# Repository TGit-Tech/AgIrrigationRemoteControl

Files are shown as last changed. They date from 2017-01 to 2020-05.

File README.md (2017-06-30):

# AgIrrigationRemoteControl
Control an Ag Industrial 3-Phase Irrigation Pump with Arduino UNO and XBee RF

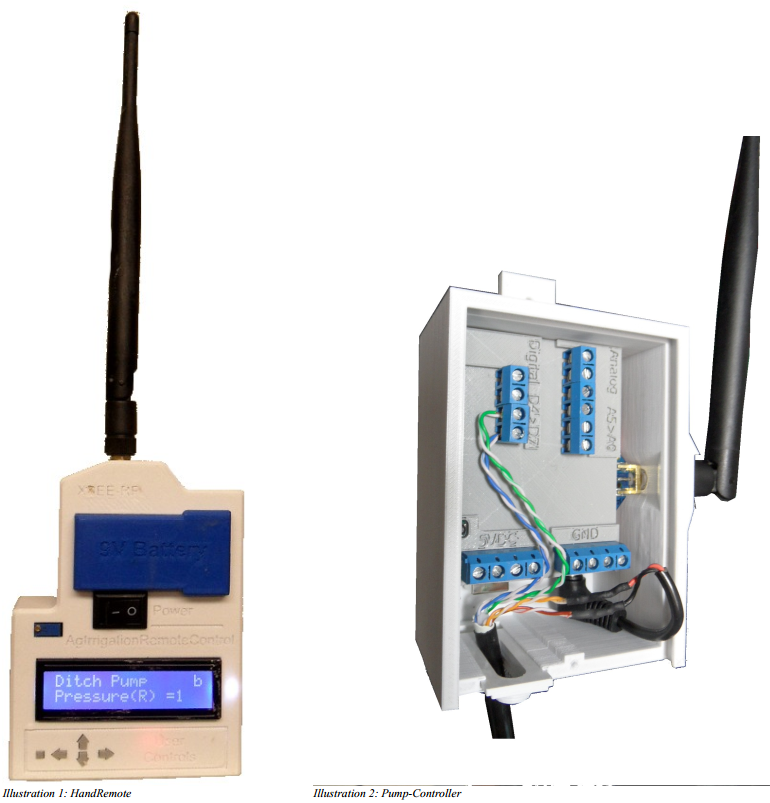
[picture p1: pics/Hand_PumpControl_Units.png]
Hand Remote

# Overview
- A solid rural 2-Mile range; possibly more ( 900MHz @ 1/4-Watt Transceiver )
- No cellular, FCC liscensing or any other charges; Just hook it up and use
- One Hand-Remote can control multiple irrigation pumps
- Multiple Hand-Remotes can control one irrigation pump
- Uses Pump Panels "AUTO" selection; doesn't disturb Manual Hand-Off & Start sequences
- Implements a "stay-off" after a power loss that is required by power companies
- Hand-Remote has settable Alarms that signal (via buzzer) unexpected conditions such as:
    - Power not as expected ( Alarms when pump shutdown has occured by a power loss )
    - Water Pressure ( if equipped ) for when a hose falls off
    - Ditch Water Level ( if equipped ) too high or low
- Simple expansion of a digital pressure gauge for water pressure monitoring
- Simple expansion of an Ultrasonic distance meter for water level monitoring

# I'll Build one for you!
I'll be building a few of these units complete with
- (1) Hand-Remote; Custom programmed to your irrigation setup
- (1) Pump-Controller; Custom programmed to your irrigation setup
- (1) Installation Kit including:
    - The required 480VAC 3-phase Power Supply
    - A 480VAC or higher Solid State Relay for Motor Starter Control
    - 600V THHN Hook-Up wire required to Motor control installation

Purchase for $329 at: https://www.etsy.com/listing/525674784/agriculture-3-phase-480vac-irrigation

If you'd like to purchase just a single unit or the Water-Level and Pressure expansion kits; you can email me directly at tgit28@gmail.com

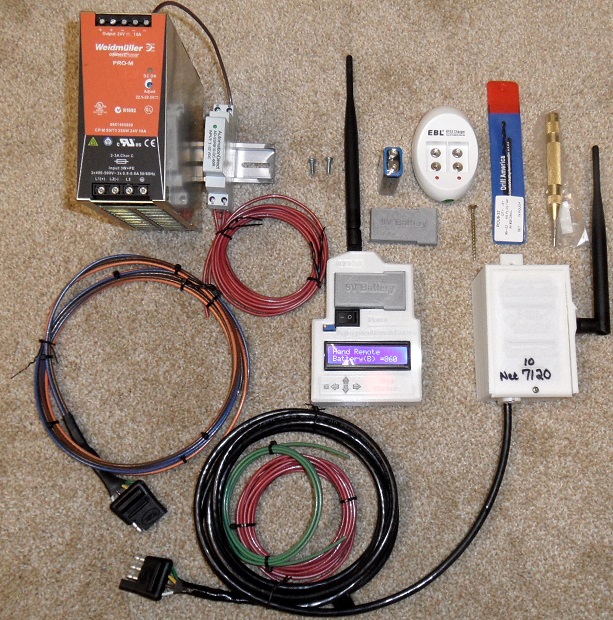
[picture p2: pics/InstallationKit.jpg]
Installation Kit


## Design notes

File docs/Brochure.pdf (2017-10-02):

# Agriculture Irrigation Pump RF Remote Control Kit

Save time changing water by Turning On and Off your irrigation pump remotely.

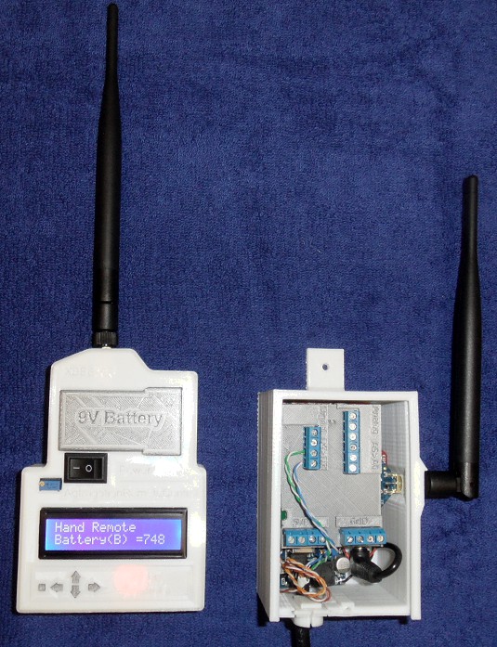
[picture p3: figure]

- Switch the pump off from the comfort of your home and wait for lines to drain before leaving.
- On the spot; Switch pump off and disconnect wheel line ends.

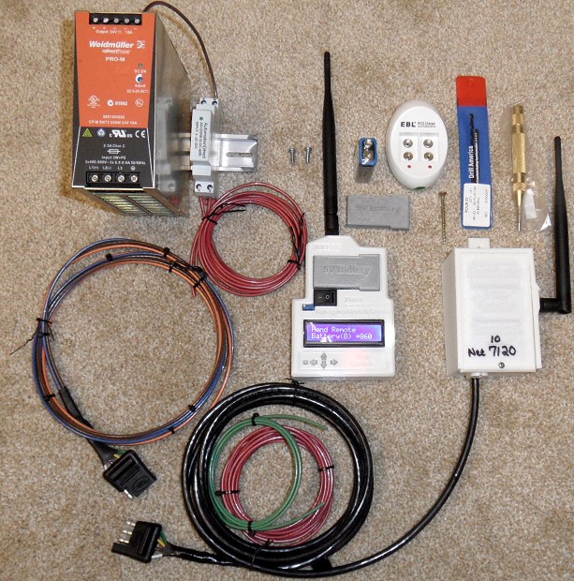
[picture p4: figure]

- Switch the pump on just as soon as
water change is complete
- On the spot pump switching for leaky drains and stubborn plugs. Simple Installation Procedure

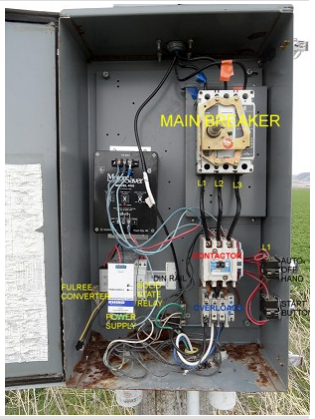
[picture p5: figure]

- Power Supply Hookup
- Solid State Relay Hookup
- Pole Mount Transceiver
- Plug-in Transceiver
- Done!

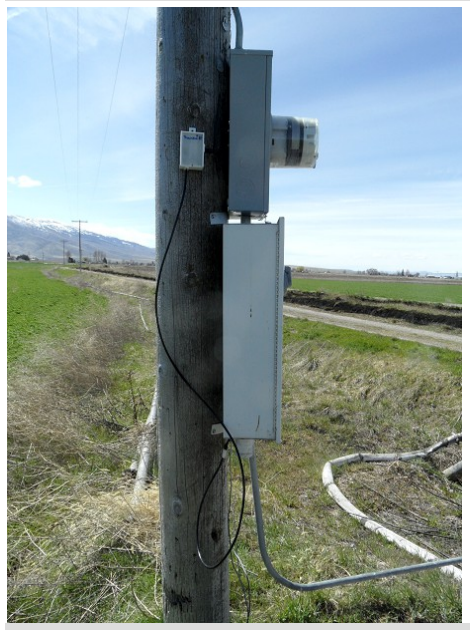
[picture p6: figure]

Easy expansion to monitor the pump 24/7
- Monitor the Water Pressure
- Monitor the Ditch Water Level
- Alarm on remote will activate when either is out of bounds.
- Special custom designs are available to suit your needs

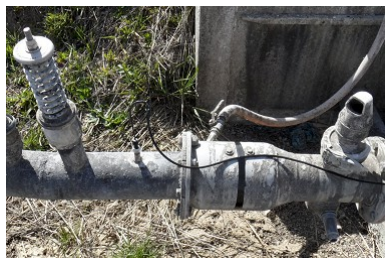
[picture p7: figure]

-----------------------------------------------------------------------------------------------------------------------------Detailed User and Installation Manual @ https://tgit23.github.io/AgIrrigationRemoteControl/manual/ Order Yours @ https://www.etsy.com/listing/525674784/irrigation-pump-remote-control-480vac-3

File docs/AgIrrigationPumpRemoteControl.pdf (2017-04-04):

# Ag Irrigation-Pump Remote Control

## Using Arduino-UNO and Digi-Xbee RF

Written By: Thomas G (01/2017) Feel free to use: no strings attached (text content only / images respectfully referenced)

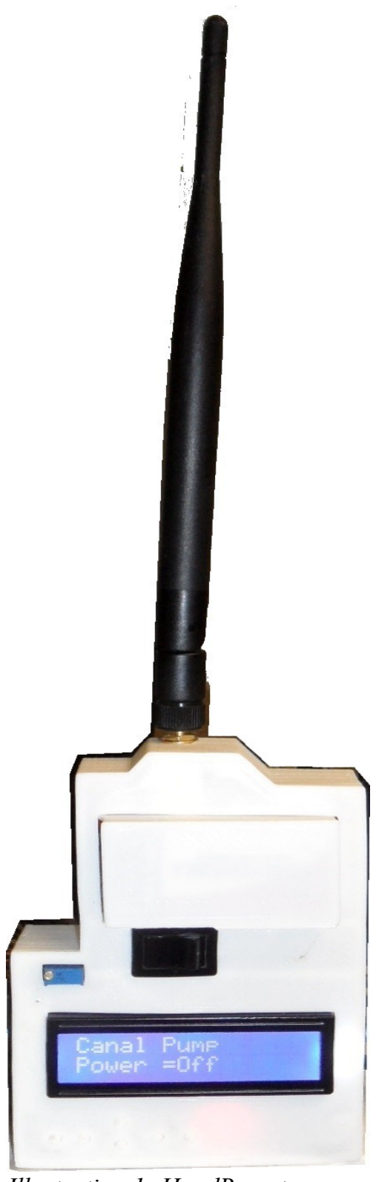
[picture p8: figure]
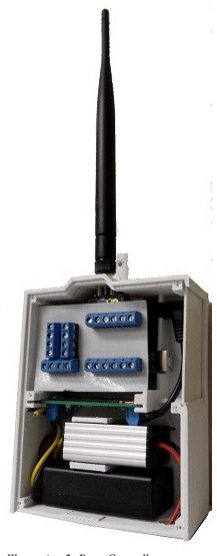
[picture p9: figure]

Illustration 1: HandRemote | Illustration 2: PumpController

# Table of Contents

( 1. INTRODUCTION :: INTRODUCTION :: INTRODUCTION ) Page -3-

### 1. INTRODUCTION

The “Ag Irrigation Pump Remote Control” project's goal is to provide RF remote control and monitoring features of an Agriculture-Industry Irrigation Pump; typically used in wheel-line and hand-line irrigation setups. The project uses Xbee RF radio's with up to a 28-mile range ( More practically a mile or two at ground level ). The project consists of a Hand-Held “Hand Remote” and a pole mounted “Pump Controller” as well as high voltage control electrical components to be added inside the pumps electrical panel.

✔ The project is Open Source and Resides at: https://github.com/tgit23/AgIrrigationRemoteControl
✔ The most recent version of this document is at: https://github.com/tgit23/AgIrrigationRemoteControl/docs/AgIrrigationPumpRemoteControl.pdf

### 1.1 Bill Of Materials (BOM) - $267.66

A. Pump-Panel Components ( $95.74 )
Illustration 3: (1) Power Supply | Illustration 4: (1) Solid State Relay | Illustration 5: (1) DIN Rail

◌ (1) 12VDC Power Supply – Main power for each PUMPCONTROLLER
- Buying Options ( Recommended; the RHINO & Fulree Converter for practical usage and pricing )
- RHINO switching Power supply, 24 VDC output, 2.5A, 60W, 320-600 VAC input, 3-phase, 35mm DIN rail mount.
- https://www.automationdirect.com/adc/Shopping/Catalog/Power_Products_(Electrical)/DC_Power_Supplies/24VDC,_3-Phase_Input/PSB24-060S-3 ( $59.00/EA )
- RHINO Requires; ( 24 12VDC ) Fulree Converter ( → | see Electronic Control Section below ) ( $7.99/EA )
- TDK Lamda Rail Power Supplies 120W 12V 10A DIN Rail 380-480VAC
- www.mouser.com/ProductDetail/TDK-Lambda/DPP120-12-3/ ( $104.04/EA )

◌ (1) Solid state relay, 35mm DIN-rail, 3-32 VDC input, SPST, normally open SCR, 10A contact rating, 48-480 VAC load voltage – for each Pump
- https://www.automationdirect.com/adc/Shopping/Catalog/Relays_-z-_Timers/Solid_State_Relays/DIN_Mount_Relays_(AD-SSR8_-z-_AD-SSR2_-z-_AD-SSR6_-z-_AD-HSSR8_Series)/Gen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,_(AD-SSR8_-z-_AD-SSR2_-z-_AD-SSR6_Series)/AD-SSR810-DC-48Z (https://www.automationdirect.com/adc/Shopping/Catalog/Relays_-z-_Timers/Solid_State_Relays/DIN_Mount_Relays_(AD-SSR8_-z-_AD-SSR2_-z-_AD-SSR6_-z-_AD-HSSR8_Seri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) ( $20.75/EA )

◌ (1) 6” of DIN rail, slotted, 35mm, 10 mm height – for mounting Power Supply and Solid State Relay of each Pump
- https://www.automationdirect.com/adc/Shopping/Catalog/Enclosures_-z-_Subpanels_-z-_Thermal_Management_-z-_Lighting/Enclosure_Subpanels_-a-_Internal_Mounting_Accessor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 (https://www.automationdirect.com/adc/Shopping/Catalog/Enclosures_-z-_Subpanels_-z-_Thermal_Management_-z-_Lighting/Enclosure_Subpanels_-a-_Internal_Mounting_A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) ( $8.00/2x 1-Meter Pieces )
B. Electronic Control ( $39.10 )
Illustration 6: (2) Arduino UNO R3 | Illustration 7: (1) LCD Keypad Shield | Illustration 8: (2) Zigbee Shield

◌ (2) UNO R3 Atmega328P Development Board with Male Pin Header and USB Cable - (1) for each HANDREMOTE and (1) for each PUMPCONTROLLER

( 1.1 INTRODUCTION :: Bill Of Materials (BOM) - $267.66 :: Bill Of Materials (BOM) - $267.66 ) Page -4-

- https://www.aliexpress.com/item/Free-shipping-high-quality-UNO-R3-MEGA328P-CH340-CH340G-for-Arduino-UNO-R3-USB-CABLE/32353698284.html ( $3.80/ea )

◌ (1) Keypad Shield Blue Backlight for Arduino Robot LCD 1602 Board – Display for each HANDREMOTE
- https://www.aliexpress.com/item/Free-Shipping1PCS-LCD-Keypad-Shield-LCD1602-LCD-1602-Module-Display-for-arduino-ATMEGA328-ATMEGA2560-raspberry-NO/32787414048.html ( $2.19 / ea )
- DFRobot Wiki LCD @ https://www.dfrobot.com/wiki/index.php/Arduino_LCD_KeyPad_Shield_(SKU:_DFR0009)
- Schematic @ http://image.dfrobot.com/image/data/DFR0009/LCDKeypad%20Shield%20V1.0%20SCH.pdf
- Layout @ https://raw.githubusercontent.com/Arduinolibrary/DFRobot_LCD_keypad/master/DFR0009_Layout.png

◌ (2) Zigbee Shield RF Wireless Module Expansion Board for Arduino Xbee - (1) for each HANDREMOTE and (1) for each PUMPCONTROLLER
- http://www.banggood.com/Zigbee-Shield-RF-Wireless-Module-Expansion-Board-For-Arduino-XBee-p-916226.htm l ( $4.83/ea )
- Schematic @ https://www.arduino.cc/en/uploads/Main/XbeeShieldSchematic.pdf
- Tutorial @ https://www.cooking-hacks.com/documentation/tutorials/xbee-arduino-raspberry-pi-tutorial/

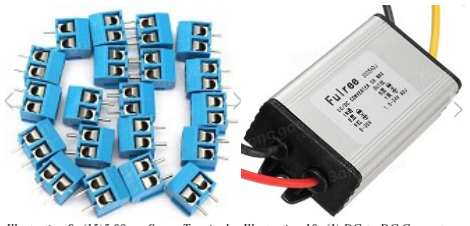
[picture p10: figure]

Illustration 9: (15)5.08mm Screw Terminal Illustration 10: (1) DC-to-DC Converter

◌ (15) 2x Pin Plug-in Screw Terminal Block Connector 5.08mm Pitch - External I/O connections for each PUMPCONTROLLER
- http://www.banggood.com/20pcs-2-Pin-Plug-in-Screw-Terminal-Block-Connector-5_08mm-Pitch-p-993197.html ( $2.15 / 20pcs )

◌ (1) Fulree DC 8-35V to 1.5-24V Adjustable Buck Converter Power Supply Voltage Regulator – For the RHINO Power Supply purchase ONLY
- http://www.banggood.com/DC-8-35V-to-1_5-24V-Adjustable-Buck-Converter-Power-Supply-Voltage-Regulator-For-Car-Truck-Boat-p-1087176.html ( Price listed with Pump Panel )
Illustration 11: Female Pin Headers | Illustration 12: Rocker Switch | Illustration 13: Active Buzzer Illustration 14: 50 / 30cm x 70cm Perfboard

◌ (4) Pin Headers 2.54mm pitch - For each PUMPCONTROLLER
- (1) 4-PIN Male | - Zigbee->Perfboard POWER ( $NA / Included with Arduino Kit - Male headers can be cut to length )
- (2) 6-PIN Male | - Zigbee->Perfboard (1) for Analog (1) for Digital ( $NA )
- (1) 4-PIN Female | - Zigbee->Perfboard RX/TX
- https://www.aliexpress.com/item/10-pcs-4P-4pin-Female-Single-Row-Straight-Header-Strip-Socket-Connector-Pitch-2-54mm/32442087495.html ( $0.79 / 10pcs )

◌ (1) Black Snap-in On/Off Rocker Switch – For each HANDREMOTE
- https://www.aliexpress.com/item/New-Black-Push-Button-Mini-Switch-6A-10A-110V-250V-KCD1-2Pin-Snap-in-On-Off/32670615106.html ( $0.86 / 5pcs )

◌ (1) Active Speaker Buzzer Alarm – For each HANDREMOTE
- https://www.aliexpress.com/item/KEYES-KY-012-Active-Buzzer-Module-FOR-The-ARDUINO-AVR-PIC/32740686896.html ( $0.60 / ea )

◌ (1) FR-4 Double Side 50cm x 70cm Prototype PCB Printed Circuit Board - (1) 50cm x 70cm for each PUMPCONTROLLER
- https://www.aliexpress.com/item/Free-Shipping-4pcs-5x7-4x6-3x7-2x8-cm-double-Side-Copper-prototype-pcb-Universal-Board-for/32730636287.html ( $1.56/ 4pcs )

( 1.1 INTRODUCTION :: Bill Of Materials (BOM) - $267.66 :: Bill Of Materials (BOM) - $267.66 ) Page -5-

◌ (2) Resistors; One valued at 1/3 the other - Recommend above 10K-Ohms – (2) for each HANDREMOTE
- http://www.banggood.com/300Pcs-1-14W-Metal-Film-Resistor-Resistance-30-Values-Assortment-Kit-p-1091920.html ( $2.28 / 300pcs )

◌ (1) Right-Angle 9Vdc Power Plug for Arduino Power Jack
- https://www.amazon.com/gp/product/B0111M6PIQ/ ( $4.51 / 10pcs )

◌ (1) Computer power connector
- http://www.banggood.com/CPU-Fan-4Pins-Patch-Cord-to-34-Pins-Power-Adapter-Cable-Lead-Wire-p-998249.html ( $1.99 / ea )

◌ (5) #4 Small Screws no longer than 10mm or bigger than 3.5mm for Display and Case covers
- https://www.boltdepot.com/Sheet_metal_screws_Phillips_pan_head_Zinc_plated_steel_4.aspx ( $0.05/ea )
C. RF Electronics ( $80.88 )

◌ (2) Xbee-Pro 900Hp S3B Digimesh, 900Mhz, 250Mw, Rpsma Connector, 200Kbps – (1) for each HANDREMOTE and (1) for each PUMPCONTROLLER
- https://www.arrow.com/en/products/xbp9b-dmst-002/digi-international ( $36.11/EA )

◌ (2) Antenna Helical 3dB Gain 900MHz – (1) for each HANDREMOTE and (1) for each PUMPCONTROLLER
- https://www.arrow.com/en/products/w1063/pulse-electronics-corporation ( $4.33/ea )
D. Wire ( $51.94 )

◌ (~10-feet) 600V 12-AWG wire for all “Inside” the Pump Panel power supply and control wiring – Enough to connect RHINO P.S., SSR and Exit Panel
- https://www.amazon.com/GREEN-12AWG-Stranded-600V-Hook/dp/B005643KCK/ref=sr_1_ 3 ( $21.99 / 25ft )

◌ (~30-feet) 24-AWG outdoor direct burial wire for Pump-Controller wiring – Enough to connect all accessory/power devices to the Pump-Controller
- https://www.amazon.com/BULKRAW-Outdoor-Outside-Waterproof-Cable/dp/B00C2J04KS/ref=sr_1_4 ( $29.95 / 40ft )

( 1.1 INTRODUCTION :: Bill Of Materials (BOM) - $267.66 :: Bill Of Materials (BOM) - $267.66 ) Page -6-

E. Tools Required ( $NA )

◌ 3D-Printer ( may be optional if other casing solutions are available ) ◌ Soldering Iron / Solder / Connecting Wire
◌ Screw Driver

### 2. HAND-REMOTE

The HANDREMOTE is the remote controller unit used to control and monitor an irrigation pump remotely.

✔ Features
◌ Buzzer alarm settings for monitored values
◌ Battery level indicator ( 9V-Battery Powered )
◌ Programmable Interface through USB

### 2.1 Electronics Assembly

✔ The HANDREMOTE uses the following electronic parts ◌ 1- Arduino UNO R3 Board
◌ 1- LCD Keypad Shield
◌ 1- Zigbee Shield
◌ 1- Xbee-Pro 900Hp S3B Module and High Gain Helical Antenna ◌ 1- 9Vdc Battery Connector
◌ 1- Active Buzzer
◌ 2- Resistors

( 2.1 HAND-REMOTE :: Electronics Assembly :: Electronics Assembly ) Page -7-

A. LCD Keypad Shield
1. Wire the Battery-Meter Voltage-Divider
a) Select (2) Resistors; One-Value being 1/3 the other ( 10K-ohm up to 1M-ohm is recommended )
b) Solder First Resistor ( Full Value ) on the top of the LCD Shield from VIN A1 →
c) Solder Other Resistor ( 1/3 Value ) from A1 GND → ( Solder hole just left of VIN )
d) Snip off the excess back-side leads

The two resistors setup a voltage divider from the 9Vdc battery (which we will attach to VIN). Analog inputs on the Arduino should never exceed 5Vdc. The voltage divider will split the battery voltage to 1/3 its actual voltage. This will allow the hand-remote to monitor the battery level. The larger the resistor values the less drain on the battery; but too-large a value resistors may affect accuracy.

2. Plug the LCD Keypad Shield onto the Arduino UNO
B. Zigbee/Xbee Shield
1. Remove Header Pin D7 From Zigbee Shield
a) Using Needle Nose pliers clamp onto Pin D7 of the back of the Zigbee Shield
b) Using Soldering Iron – Heat the top of the pins solder pad and pull the pin from the board

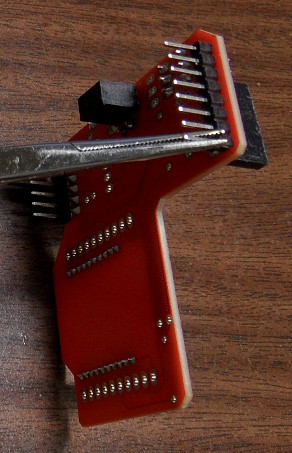
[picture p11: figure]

2. Solder Zigbee Shield to the LCD Keypad ( Flipped upside down )
a) Insert pins D0 D6 ( D7 removed in Step #1 ) into the Top Solder holes of the LCD Keypad Shield →
b) Position the Zigbee Shield flat with LCD Shield and Up against the LCD Shield – Requires bending the header pins a little ( with UNO Attached )
c) Solder the Zigbee pins to the LCD Keypad Shield

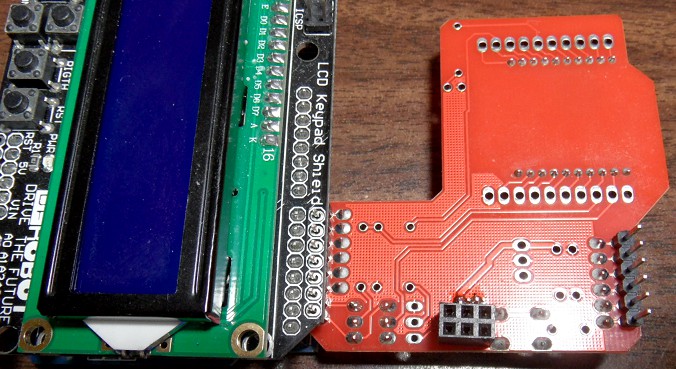
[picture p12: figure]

( 2.1 HAND-REMOTE :: Electronics Assembly :: Electronics Assembly ) Page -8-

✔ Further Reading for the Curious
- https://www.arduino.cc/en/Main/ArduinoXbeeShield
- https://www.arduino.cc/en/Guide/ArduinoXbeeShield
C. Active Buzzer
1. Solder Active Buzzer to LCD Keypad Shield
a) Either print a small piece of plastic or add Black tape to the Back-Side of the Active Buzzer to prevent shorting against the Zigbee Shield.
b) Solder the 'S' pin on the Active Buzzer to D2 ( 3rd Left Pin – LCD Face Up ) on the LCD Shield
c) Cut the (-) and center pins of the Active Buzzer leaving about 1/8” for connection but short enough not to touch D3 & D4.

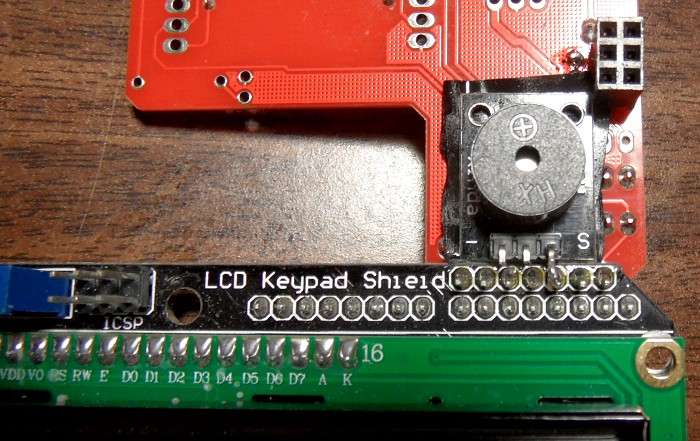
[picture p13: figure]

( 2.1 HAND-REMOTE :: Electronics Assembly :: Electronics Assembly ) Page -9-

2. Wire Power to the Active Buzzer and Zigbee Shield
a) Bend the first and last pins closest to the edge of the LCD Keypad Shields ICSP pin header
b) Solder one end of a Red wire Left-Most Pin of the LCD Keypad Shields ICSP pin header ( → | 5V+)
- Pull wire to Active Buzzer (+) Pin ( Center Pin ), strip insulation and solder
- Pull wire to Lower-Right of the Zigbee ICSP ( 5V+ ) plug, strip insulation, cut to length and insert into plug
c) Solder one end of a Black wire Right-Most Pin of the LCD Keypad Shields ICSP pin header ( → | 5V+)
- Pull wire to Active Buzzer Left-Pin (-), strip insulation and solder
- Pull wire to Top-Right of the Zigbee ICSP ( GND ) plug, strip insulation, cut to length and insert into plug

Red/Black wires were not cut but the insulation was split using automatic wire strippers. The Center and Left Pins of the Buzzer were cut just long enough to solder wires to them.

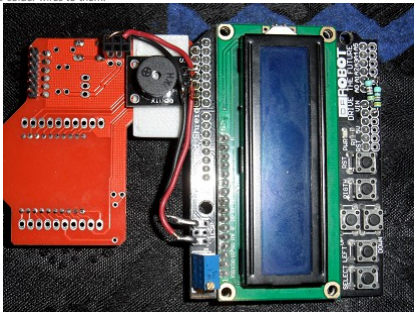
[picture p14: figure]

3. Cut the remaining ICSP pins as short as possible to allow the unit to fit inside the case
D. Communications

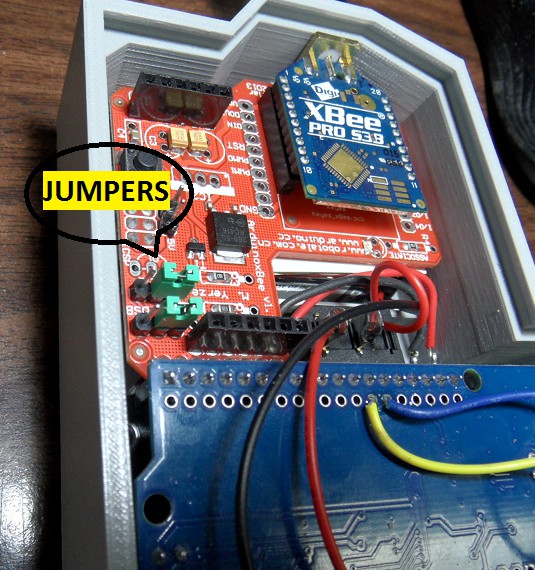
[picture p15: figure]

1. Remove the two green jumpers factory installed on the Zigbee shield

( 2.1 HAND-REMOTE :: Electronics Assembly :: Electronics Assembly ) Page -10-

2. Connect Arduino UNO pins D11 & D12 to the Zigbee Communication Header
a) From an upside-down view; left-top of Arduino UNO; Count the pin holes to the right D0,D1,D2.... to D11
b) Solder a wire from Arduino UNO pin D11 to the top-jumper-header center-pin of the Zigbee shield
c) Solder a second wire from Arduino UNO pin D12 to the bottom-jumper-header center-pin of the Zigbee shield

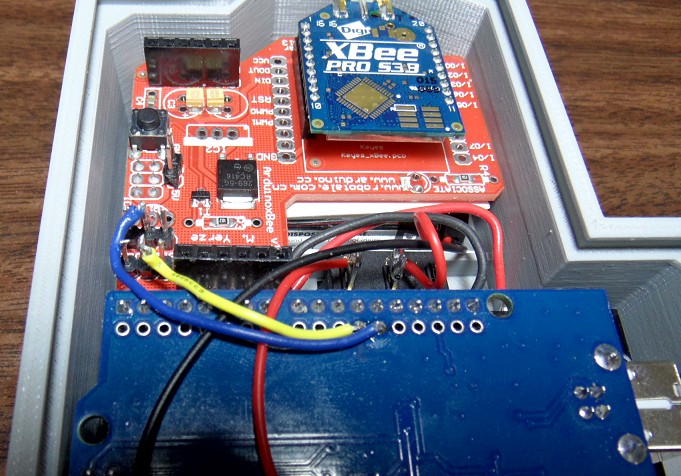
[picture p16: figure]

✔ Further Details for the Curious

◌ Xbee and Arduino both use Serial Communications –- but they both cannot use the same Serial Port at the same time.
- In order to Upload Firmware to the Arduino the Xbee must be disconnected from the lines ( No Jumpers )
- In order to Connect to the Xbee through USB Serial the Arduino Microcontroller must be disconnected ( UN-usable for our Arduino UNO )
- Thus; We add Jumper-wires to put the Xbee on a different “Serial Port” when we need access to both Serial Devices.

◌ The Factory Jumpers on the Zigbee Shield come with two modes of operations
- Xbee Position = Xbee UART Serial connects to Arduino Serial
- USB Position = Xbee UART Serial connects to USB Serial ( Computer ); Requiring the removal of the micro-controller.

◌ Jumper-Wires for Debug
- Computer USB Serial Arduino → | - When NO jumpers exist; the Xbee is disconnected from RX/TX Pins and thus allows clean USB Serial Monitor.
- Routes Xbee UART D11 & D12 → | - The SOFTWARESERIAL Library allows UART communications on D8 & D9 which is wire-jumped to the Xbee RX/TX.

◌ Pin Orientation
- The Jumpers on the Zigbee Shield are aligned Top->Bottom Exactly the same as the Xbee Plug labeled DIN/DOUT are aligned
- On the shield (DIN is the closest jumper to Digital Pins Header on the Shield)

( 2.2 HAND-REMOTE :: Hardware Assembly :: Hardware Assembly ) Page -11-

### 2.2 Hardware Assembly

A. 3D-Prints
✔ Print the Following Models on a 3D-Printer
◌ /HandRemote/3D-Prints-STL/HandRemote-Case.stl
◌ /HandRemote/3D-Prints-STL/HandRemote-Buttons.stl
◌ /HandRemote/3D-Prints-STL/HandRemote-BackCover.stl
◌ /HandRemote/3D-Prints-STL/HandRemote-BatteryCover.stl
◌ /HandRemote/3D-Prints-STL/HandRemote-BatteryInsulatorPlate.stl ◌ /HandRemote/3D-Prints-STL/HandRemote-SideCover.stl
Illustration 15: Case.stl | Illustration 16: BackCover.stl | Illustration 17: Battery Cover
Illustration 18: BatteryInsulatorPlate.stl | Illustration 19: SideCover.stl | Illustration 20: Buttons.stl
B. Install Electronics
1. Insert the Power ON/OFF Rocker Switch into the front of the case
2. Place the buttons in their proper place inside the case; using masking tape on the front-side to hold the buttons in their place

( 2.2 HAND-REMOTE :: Hardware Assembly :: Hardware Assembly ) Page -12-

3. Install the LCD, Buzzer, Zigbee Electronics Assembly ( from Step #2.1 ) into the Case ( Arduino UNO Removed )
a) Insert (4) 10mm or shorter screws – adjust tightness making sure the buttons still click ( too tight will pinch buttons down permanently )

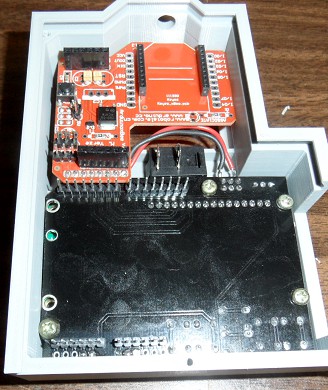
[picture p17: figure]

4. Plug the Arduino UNO back onto the LCD Keypad Shield
5. Slide the Xbee into the Top-Hole and then plug into the Zigbee Shield
6. Attach the Antenna to the Xbee RPSMA Connector
C. Wire in Battery Power
1. Install Plugs
a) Insert the HANDREMOTE-BATTERYINSULATORPLATE.STL 3D-Print inside the battery hole
b) Route the 9Vdc Battery Power Plug from the front, around Zigbee shield, to the back

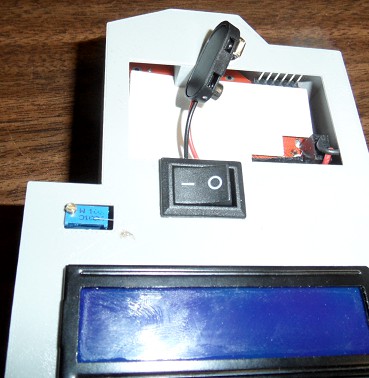
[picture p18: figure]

( 2.2 HAND-REMOTE :: Hardware Assembly :: Hardware Assembly ) Page -13-

2. Wire in the Switch and Power to the Arduino UNO
a) Solder the Black wire to the closest to UNO power-jack backside pin ( as pictured )
b) Leaving an inch-or-so slack on the 9VDC plug; measure and cut the Red wire on the closest rocker-switch connector
c) Strip the end and solder the wire to the rocker switch connector
d) Strip the end of the cut left-over red wire and solder it into the “other” connector on the rocker-switch
e) Solder the other end of the cut left-over red wire wire to the farther to UNO power-jack backside pin ( as pictured )

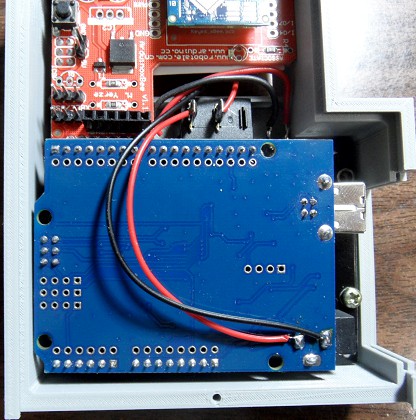
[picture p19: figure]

3. Check for Power
a) Plug in a 9V-Battery into the 9V plug
b) Flip the rocker-switch to power-on ( marked with a “-” ) and verify that the LCD display lights
4. Attach Covers to Case
a) Insert the HANDREMOTE-BATTERYCOVER.STL 3D-Print into the cases battery-hole and snap down
b) Slide the HANDREMOTE-BACKCOVER.STL 3D-Print in from the bottom then insert a screw in the bottom-center
c) Slide the HANDREMOTE-SIDECOVER.STL 3D-Print in the USB side until it snaps into place

### 2.3 Operating Instructions

Notice: Firmware must be uploaded to a newly assembled unit before it can operate; visit #4.1.A SYSTEM OPERATIONS| Firmware | Uploading for details
A. Introduction

The main screen has “Menu Items” like Pump, Power, Water Level, Battery Level, Water Pressure and etc..
After the unit is idle (No buttons pressed) for a time - The “Menu Items” will iterate and items value will be retrieved from the Pump-Controller.
MENU ITEM | SET | PIN | LOW ALARM | HI ALARM
Pump | Canal/Ditch (Options) | PumpID | Equals (=) | NOT Equal (ǂ)
Power | ON/OFF (Options) | D7 | Equals (=) | NOT Equal (ǂ)
Water Level | DISABLED | V64(Trig=D6,Echo=D5) | Less Than (<) | Greater Than (>)
Battery | DISABLED | A2 | Less Than (<) | Greater Than (>)
Pressure | DISABLED | A3 | Less Than (<) | Greater Than (>)

( 2.3 HAND-REMOTE :: Operating Instructions :: Operating Instructions ) Page -14-

* Note: V64 is Virtual Pin #64; Virtual Pins are memory spaces inside the Pump-Controller and therefore the Pump-Controller firmware actually identifies the connecting pins. This is used when Pump-Controller processing is done before a legitimate value can be determined.

B. Pump Control
To Set the Pump-Controller the Hand-Remote will communicate with; press the UP/DOWN until Menu Item “Pump” is selected.
Then press the RIGHT to SET the pump.
Then press UP/DOWN to select the desired Pump-Controller
Then press the SQUARE ( Select ) button to actually SET the pump selected.
C. Alarms
D. Customizing

( 3. PUMP-CONTROLLER :: PUMP-CONTROLLER :: PUMP-CONTROLLER ) Page -15-

### 3. PUMP-CONTROLLER

✔ Automation
◌ Automatically turn off the pump if no water exists
◌ Set to Automatically turn on pump when water height is okay
Wiring Diagram of the PUMP CONTROLLER - ( Screw Terminal Perfboard Zigbee Shield Arduino UNO → | → | )

### 3.1 Perfboard Assembly

1. Install Headers
a) Remove outer pins on one 4-PIN female header ( POWER )
b) Remove every other pin on one 4-PIN female header ( RX/TX )

( 3.1 PUMP-CONTROLLER :: Perfboard Assembly :: Perfboard Assembly ) Page -16-

c) Remove the (2) Green Jumpers on the Zigbee Shield and plug it onto the Arduino UNO
d) Plug a 6-Pin Male Header into the Analog Header of the Zigbee Shield ( A5 A0 ) →
e) Plug a 6-Pin Male Header into the Digital Header of the Zigbee Shield ( D2 D7 ) →
f) Insert the POWER female header from step #a into the Zigbee Shield holes labeled 5V & GND ( next to the reset button )
g) Plug a 4-Pin Male Header into the top of the POWER female header
h) Insert the RX/TX female header from step #b ACROSS the two center male header (XBEE/USB) pins of the Zigbee Shield

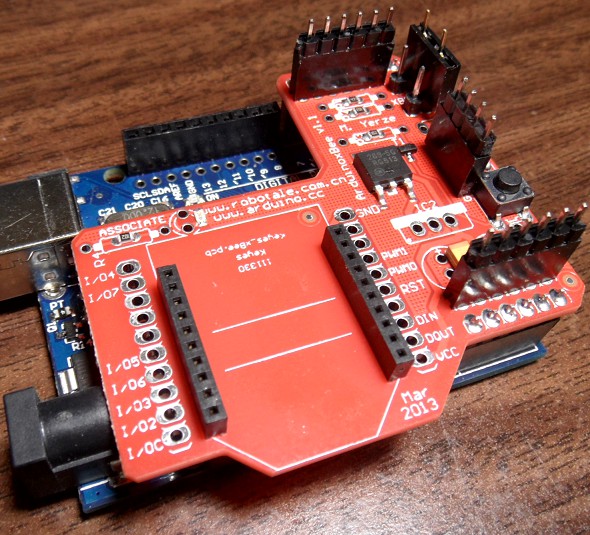
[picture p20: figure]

2. Solder the header pins to a 5cmx7cm 2.54mm pitch Perfboard
a) Align and place the Perfboard onto the header pins
b) Solder the header pins to the Perfboard

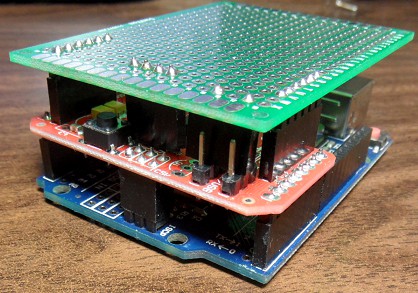
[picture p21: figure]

3. Solder the Zigbee female POWER header pins
a) Unplug the Arduino UNO from the Zigbee Shield leaving the Perfboard attached
b) Solder the female POWER header pins to the holes of the Zigbee shield

( 3.1 PUMP-CONTROLLER :: Perfboard Assembly :: Perfboard Assembly ) Page -17-

4. Add wires to the header pins
a) Cut (12) wires approximately 1” long and strip one end.
b) Cut (2) wires approximately 3” long and strip one end.
c) Unplug the Perfboard from the Zigbee Shield
d) Insert (6) 1” wires from the Zigbee-side of the Perfboard into the holes just below the analog male pin headers, bend and solder
e) Insert (4) 1” wires from the Zigbee-side of the Perfboard into the 4-right (D4-D7) holes just above the digital male pin headers, bend and solder
f) Insert (2) 3” wires from the Zigbee-side of the Perfboard into the right of the POWER male pin headers ( Center-2 ), bend and solder
g) Attach (2) 1” wires from the Top-side of the Perfboard across RX/TX female pin headers and solder to D3, D4 Digital pins as shown and trim.

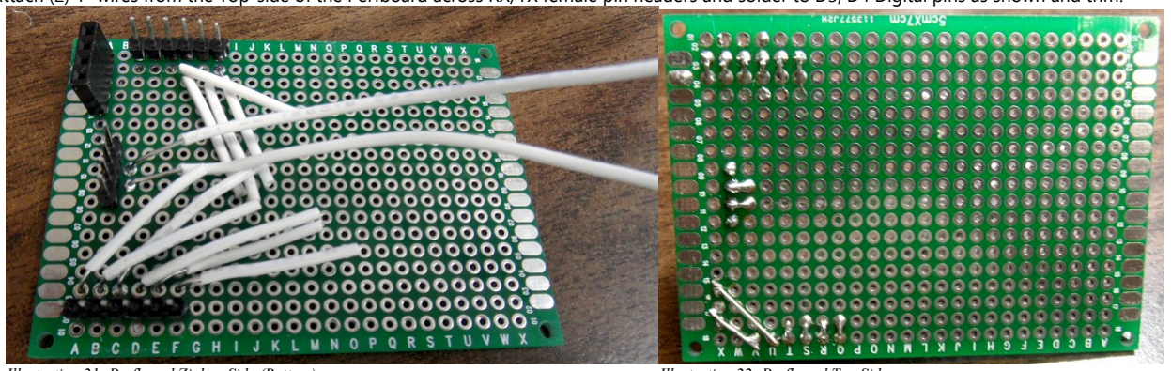
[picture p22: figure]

Illustration 21: Perfboard Zigbee-Side (Bottom) | Illustration 22: Perfboard Top-Side
5. Install the Screw Terminals
a) Place the HANDREMOTE-PERFBOARDCOVER.STL 3D-Print on the top of the Perfboard lining up grooves with header pin solder joints
b) Insert (3) 2x Screw Terminals along the Analog section starting at the Right and working left to allow sliding the blocks together at their edges
c) Insert (2) 2x Screw Terminals along the Digital section with the same method above
d) Insert (2) 2x Screw Terminals along the 5VDC section ( same as above )
e) Insert (2) 2x Screw Terminals along the GND section ( same as above )

( 3.1 PUMP-CONTROLLER :: Perfboard Assembly :: Perfboard Assembly ) Page -18-

6. Solder the Screw Terminals to their corresponding header wires
a) Turn the Perfboard over holding the screw terminals into place
b) Sold each screw terminal pin to the Perfboard
c) Pull the Insulation off the wires, bend them flat with the Perfboard and solder them to their corresponding pin ( See picture or Wiring Diagram )

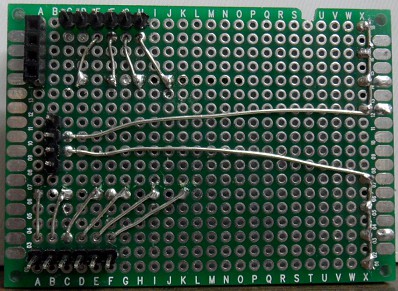
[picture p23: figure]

### 3.2 Hardware Assembly

A. Print Models (3D-Prints)

✔ 3D-Print the Following Models @ https://github.com/tgit23/AgIrrigationRemoteControl/tree/master/PumpController/3D-Prints-STL ◌ PumpController-Case.stl
◌ PumpController-Cover.stl
◌ PumpController-USBCover.stl
◌ PumpController-AntennaCover.stl
Illustration 23: Case.stl | Illustration 24: Cover.stl | Illustration 25: USBCover.stl | Illustration 26: AntennaCover.stl

( 3.2 PUMP-CONTROLLER :: Hardware Assembly :: Hardware Assembly ) Page -19-

B. Install Electronics
1. Install UNO and Zigbee connected into the Case
a) Remove the Screw Terminal Perfboard if attached and connect the Arduino UNO & Zigbee Shield
b) Plug in the Right-Angle 9Vdc Power Plug for Arduino Power Jack
c) Insert the Uno/Zigbee assembly into the case letting the USB and power Jack sit on each side of the case stub.

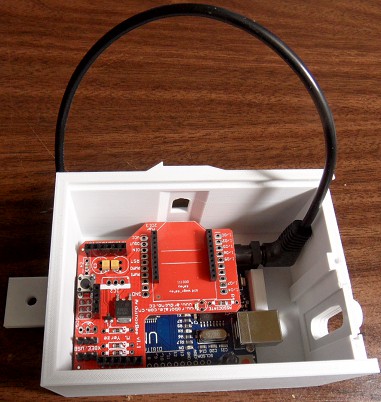
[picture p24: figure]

2. Install the XBEE module
a) First slide the XBEE RPSMA Connector into the case slot
b) Then lift the XBEE module into to place and plug it into the Zigbee Shields Xbee plug-in

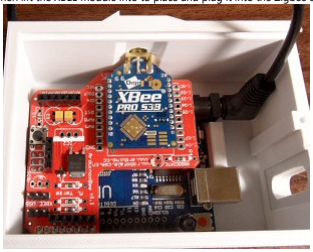
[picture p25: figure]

3. Install the Xbee Antenna Cover
a) Slide the ANTENNACOVER.STL 3D-Print onto the RPSMA connector from the outside of the case

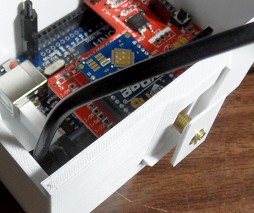
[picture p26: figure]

( 3.2 PUMP-CONTROLLER :: Hardware Assembly :: Hardware Assembly ) Page -20-

b) Attach the washer and nut and tighten


4. Plug the Perfboard into the Zigbee shield

### 3.3 Installation Instructions

### 3.3.1 Prepare for Installation

A. DIN Rail Components
1. Cut to Length a portion of DIN Rail
a) A length that will comfortably fit the Power Supply, Solid State Relay, and Fulree DC/DC Converter
b) A length that will fit comfortably somewhere inside the Pump Power Panel
c) Recommending approximately 5-1/2” or 4-hole slots in length
2. Wire RHINO power supply to Fulree DC/DC Converter
a) Attach the RED(+) IN wire of the Fulree DC/DC Converter to the RHINO power supply at the top labeled ( 24VDC+ )
b) Attach the BLACK(-) IN wire of the Fulree DC/DC Converter to the RHINO power supply at the top labeled ( 24VDC- )
3. Wire GND to the Solid State Relay
a) Attach a wire ( Recommend BLACK or GREEN ) from the “other” 24VDC- on top of the RHINO power supply to A1 of the Solid State Relay
B. Pump-Controller Power Cable
1. Select a place to mount the Pump-Controller on the Pole next to the Pumps electrical panel
a) Measure and cut a length of Cat5e outdoor cable to reach from that spot to the bottom of the electrical panel
2. Create Cable to connect the PUMP-CONTROLLER → PUMP-PANEL- EXIT PLUG which will be installed in 3.3.2-Section D-Step#3
a) Separate the two connecting ends of a Computer power plug ( shown in the BOM ) by cutting the wires in the middle
b) Wire up the MALE end of the cable and save the FEMALE end for the PUMP-PANEL- EXIT PLUG
- Strip the wire ends of the Cat5e twisted pair wires
- Strip the wire ends of the male Computer power plug
- Solder the Computer power plug to the twisted pair wires as shown
- Yellow power plug Orange twisted pair → | ( 9Vdc+ )
- Black next to Yellow power plug Brown twisted pair → | ( 9Vdc GND )
- Black next to Red power plug Green twisted pair → | ( Extra Accessory Wire )
- Red power plug Blue twisted pair → | ( Pump Control )


( 3.3.1 PUMP-CONTROLLER :: Installation Instructions :: Prepare for Installation ) Page -21-

c) Wire up the Pump-Controller end ( Other end of the same wire in step#a above )
- Strip the outer insulation from the Cat5e Cable approximately 4” from the end
- Strip and wire the twisted pairs as follows
- Orange twisted pair Red wire of the angled 9Vdc UNO Power plug →
- Brown twisted pair Black wire of the angled 9Vdc UNO Power plug →
- Green twisted pair Perfboard screw terminal ( D6 ) →
- Blue twisted pair Perfboard screw terminal ( D7 ) →

### 3.3.2 Wiring Power & Control

This section is a guide to installing the required power supply and pump ON/OFF switching mechanisms inside the pumps electrical panel.

✔ The following SUPPLIES will be needed
◌ DIN Rail cut to length ( Recommend 5-1/2” )
◌ The RHINO Power Supply
◌ The Fulree DC/DC Converter mounted to the PUMPCONTROLLER-FULREEDINMOUNT.STL 3D-Print ◌ The Solid State Relay
◌ 12-Gauge wire rated at 600V or more

✔ The following TOOLS will be needed
◌ Voltmeter that reads up to or beyond 500VAC ◌ Cordless drill
◌ Center tap
◌ Bit ( #21 for #10-32 Machine Screw )
◌ Threading tap ( #10-32 for #10-32 Machine Screw )
◌ (2)-Machine Screws
◌ Protective insulated and flash protection personal gear
◌ Wire strippers and cutters

BE SURE THE MAIN BREAKER IS TURNED OFF AND CAREFULLY CHECK THAT THERE IS NO VOLTAGE ON THE OUTPUT OF THE MAIN BREAKER WITH A PROPER METER!!! 480VAC is deadly; and can cause severe flash burn and/or death. (e.g. A meter on the wrong setting can “flash” explode causing “flash” burns on you even at a distance away). I DISCLAIM ANY AND ALL RESPONSIBLITY FOR ANY RISK OR HARM OCCURED BY FOLLOWING ANY INSTRUCTION IN THIS MANUAL.
See https://www.youtube.com/watch?v=6hpE5LYj-CY
A. Observe Pumps Electrical Panel
Most 3-phase irrigation pumps that do not have variable frequency drives(VFD) or inverters are setup similarly. Below is the details of two pump panels as an example or reference to the pumps power circuit. This information was gathered to determine the wiring and power needed to control the pumps power.

( 3.3.2 PUMP-CONTROLLER :: Installation Instructions :: Wiring Power & Control ) Page -22-

✔ Details

◌ Box | - Eaton Irrigation Pump Control Type 3R Enclosure Rainproof
- http://www.eaton.com/Eaton/ProductsServices/Electrical/ProductsandServices/AutomationandControl/EnclosedControl/NEMA/PumpPanels/index.htm


◌ Wiring Diagram Description
- Labels
- L1, L2, L3 | - Are the three HOT wires of the 3-Phase Power
- M | - The Starter Contactor ( see Panel picture; white block with a blue center ) contains:
- Activation Coil | - Shown as a circle in the wiring diagram just right of the Start Button ( Activates the “Hammer” )
- Main Contacts | - The Contacts that connect the L1,L2,L3 lines OL Motor ( Sometimes called the “Hammer” ) → | →
- Hold Contact | - The Contact wired in parallel with the Start Button and mounted on the Right-Side of the Starter Contactor Block

When HAND is selected the “control circuit” ( L1 L2 loop ) is still open until the Start Button is pressed. When the Start button is pressed it → activates the (M) Coil which in-turn activates the “Hold Contact” ( the --| |-- in parallel to the Start Button). This right-side contactor holds the “control circuit” closed until there is a power failure bump or the Hand-Off-Auto Switch breaks open the circuit loading the (M) activate coil.

This Projects SSR-Relay will be connected where the “Pressure Switch” is shown in this wiring diagram and will use the AUTO switch selection. This setup will require that the Arduino NOT re-activate power after a power failure has occurred until a specified time delay or turned back on. The click in HAND circuit is setup so the power company can re-activate power after a power failure without the over-load of all motors kicking on at the same time.

◌ Starter Contactor | - Eaton-Cuttler/Hammer 45-Amp Model # AN16GNO Series B1 | ( Need to check Contactor Model # )
- MODEL # Decoding
- A = Starter
- N = NEMA
- 1 = Non-Reversing
- 6 = Starter w/C306 Over Load Relay
- G = NEMA Size #2 ( 45-Amp )
- N = Normally Open
- O = Horizontal Mount
- https://www.galco.com/buy/Cutler-Hammer-Div-of-Eaton-Corp/AN16GN0AB
- http://www.eaton.com/Eaton/index.htm
- http://www.eaton.com/Eaton/ProductsServices/Electrical/ProductsandServices/AutomationandControl/ContactorsStarters/ElectromechanicalContactorsandStarters/FreedomSeri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 (http://www.eaton.com/Eaton/ProductsServices/Electrical/ProductsandServices/AutomationandControl/ContactorsStarters/ElectromechanicalContactorsandStarters/Free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)

( 3.3.2 PUMP-CONTROLLER :: Installation Instructions :: Wiring Power & Control ) Page -23-

◌ Starter Contactor (Coil) Amperage
- See Page 9 “AC COIL DATA” for NEMA Size #2 Shows 230VA(Volt-amperes which is VA=V*A) so 230VA/480Vac = 0.479Amps @ 480V
- http://www.eaton.com/ecm/idcplg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 (http://www.eaton.com/ecm/idcplg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)
◌ Auxiliary Contact - Cutler Hammer Model #C320KGS1 10-Series A2 ( 480VAC @ 1.5 Amps? )
B. DIN-Rail Components
1. Drill two holes in desired location, punch, tap-thread, and mount the DIN rail horizontally
a) Recommend using a #10-32 x 1/2” Machine Screw
b) Drill bit size for #10-32 is #21 – 5/32” - 0.1590”
2. Snap on the RHINO power supply to the DIN rail in the center
3. Snap on the Solid State Relay to the DIN rail on the right of the RHINO power supply
4. Snap on the Fulree DC/DC Converter to the DIN rail to the left of the RHINO power supply


C. Pump Panel wiring

NOTICE: All wiring in this section should be done with 600V rated wire

( 3.3.2 PUMP-CONTROLLER :: Installation Instructions :: Wiring Power & Control ) Page -24-


1. Wire the RHINO Power Supply
a) Connect RHINO terminal L1, L2, L3 to the top terminals of the Contactor ( i.e. Starter / Hammer ) L1, L2, L3 terminals
b) Connect RHINO GRND terminal to a bold on the panels back-plane
2. Wire the Solid State Relay
a) Connect Solid State Relay (15) → AUTO Terminal of the HAND-OFF-AUTO switch
b) Connect Solid State Relay (16) Contactor Activation Coil side connected to the Auxiliary Contact & Start Button ( BUT NOT THE HAND SIDE ) →
3. Wire in the female Exit Plug
a) With the Female end of the Computer power plug from 3.3.1.A Exit Plug insert wires through a bottom hole in the Pumps Electrical Panel
b) Connect the Yellow & Black wires from the Fulree DC/DC converter to the Yellow/Black wires of the female end of the Computer power plug
c) Connect the Solid State Relay (A2) to the RED wire of the female end of the Computer power plug
d) Tape off the Black wire next to the Red wire ( Can be used as with an “optional” auxiliary contact to verify pumps power status )

( 3.4 PUMP-CONTROLLER :: Optional Accessories :: Optional Accessories ) Page -25-

### 3.4 Optional Accessories

A. Power Alternatives

✔ Car Battery for Main Pump-Controller Power ( Currently No Implementation Plan )
◌ Requires an auxiliary contact to monitor the Pumps power source so the pump can wait a while after a power bump to restart the pump.

✔ Emergency Backup 9V Battery Power ( Currently No Implemented Plan )
◌ Requires either
- An auxiliary contact to monitor the Pumps power source
- A voltage monitor that can determine when the emergency power has started and the Pumps power source is gone. ◌ Advantages
- Allows reading of water levels during a power outage
- Allows ( though risky ) the automatic restarting of the pump once power is restored
- The case is already designed to hold a 9VDC Battery Case

** After considering the benefit and risk the back-up power implementation plan was canceled for the time being

B. Pressure Transducer ( $9.59 )

✔ 5V 0-1.2 MPa Pressure Transducer Sensor Oil Fuel Diesel Gas Water Air Sensor
◌ http://www.banggood.com/Pressure-Transducer-Sensor-Oil-Fuel-Diesel-Gas-Water-Air-Sensor-p-1007341.html | - $9.59

Wiring: red +, black -, yellow output
C. Ultrasonic Water Level ( $10.77 )

✔ DC 5V Waterproof Ultrasonic Module Distance Measuring Transducer Sensor
◌ http://www.banggood.com/DC-5V-Waterproof-Ultrasonic-Module-Distance-Measuring-Transducer-Sensor-p-1094462.html | - $ 10.77

✔ Benefits
◌ Offers a way to monitor the water level in a ditch

( 3.4 PUMP-CONTROLLER :: Optional Accessories :: Optional Accessories ) Page -26-

D. Auxiliary Contact ( $43.75 )

✔ Auxiliary contact, side mounted, 1 N.O. Contact ( NOTE: This must match/fit the pump panels Contactor Unit )
◌ https://www.automationdirect.com/adc/Shopping/Catalog/Motor_Controls/Eaton_Cutler-Hammer_Contactors_-z-_Starters_-z-_Overloads/Auxiliary_Contacts/C320KGS1 - $43.75/ea

✔ Notes
◌ Auxiliary Contactor must be purchased according to the contactor they will FIT on.
- The above suggested purchase will ONLY work with the NEMA-2 Model # AN16GNO Series B1 Contactor
◌ The Auxiliary Contactor typically already used by the Start-lock CANNOT be used for this purpose as it has 480V wires already attached to it. ◌ Often a used aux contactor can be found much cheaper on ebay

✔ Benefits
◌ Offers a way to monitor the actual (i.e. directly) the pump power status
E. Water Meter

( 4. SYSTEM OPERATIONS :: SYSTEM OPERATIONS :: SYSTEM OPERATIONS ) Page -27-

### 4. SYSTEM OPERATIONS

### 4.1 XBEE Setup

The XBEE RF Module is setup from the factory to work without any additional changes. However, often it is very wise to assign non-factory setting in order to keep your RF communications from being interfered with by other XBEE devices in the neighborhood.

1. Upload Firmware with XBEE Configuration Set
a) To change the XBEE settings – Follow Steps #1 to #3 in #4.2.A SYSTEM OPERATIONS|Firmware|Uploading

With the Firmware file open find the following line of code which should be very close to the top

#define XBEECONFIG 0 | // 1 to enter XBEE Configuration Mode

Change to

#define XBEECONFIG 1 | // 1 to enter XBEE Configuration Mode

b) Then proceed to upload the firmware to the Unit as outline in Step #4 in #4.2.A SYSTEM OPERATIONS|Firmware|Uploading
2. Install Digi-XCTU
a) The Digi XCTU software can be gotten from https://www.digi.com/products/xbee-rf-solutions/xctu-software/xctu
3. Run Digi-XCTU
a) Using the + mark in the top left corner enter the unit's COM port ( The Arduino COM Port )
b) The main values that may be of interest are:
- ID Network ID - This sets a Unique “Channel” to keep your units communications separate from any others out there (Must be same on all units)
- PL TX Power Level - If devices are close; a lower power setting can preserve battery life
4. Save Settings to the Xbee and Reload Firmware
a) Be sure to click the “Write” button in XCTU to save any settings that were made
b) Close XCTU
c) In Arduino Sketch IDE restore the following line to its original
#define XBEECONFIG 0 | // 1 to enter XBEE Configuration Mode

d) Upload the Firmware to the Unit again as outline in Step #4 in #4.2.A SYSTEM OPERATIONS|Firmware|Uploading

### 4.2 Firmware

( 4.2 SYSTEM OPERATIONS :: Firmware :: Firmware ) Page -28-

A. Uploading
1. Install Arduino Sketch IDE ( If NOT installed already ) | https://www.arduino.cc/en/Main/Software
2. Install the PEERIOSERIALCONTROL Library | ( If NOT installed already )
a) In a web-browser; go to https://github.com/tgit23/PeerIOSerialControl
b) On Green CLONE OR DOWNLOAD Choose DOWNLOAD ZIP
c) Save to a place you'll remember – like Documents or Desktop
d) Run the Arduino Sketch IDE
e) Choose Menu Item SKETCH → INCLUDE LIBRARY → ADD .ZIP LIBRARY
f) Select the PEERIOSERIALCONTROL Library file saved in step 'b' above
3. Download the Firmware
a) In a web-browser; go to https://github.com/tgit23/AgIrrigationRemoteControl
b) On Green CLONE OR DOWNLOAD Choose DOWNLOAD ZIP
c) Save to a place you'll remember – like Documents or Desktop
d) Unzip the Folder
e) In Arduino Sketch IDE choose FILE → OPEN and Select
- File HANDREMOTE.INO for the HANDREMOTE Firmware
- Location Example: \Downloads\AgIrrigationRemoteControl-master\AgIrrigationRemoteControl-master\HandRemote
- File PUMPCONTROLLER.INO for the PUMPCONTROLLER Firmware
- Location Example: \Downloads\AgIrrigationRemoteControl-master\AgIrrigationRemoteControl-master\PumpController\PumpRemote
4. Compile and Upload the Firmware
a) Setup the unit to “Upload-Mode” by removing both Zigbee Shield jumpers
b) Plug in a USB cable from the Computer to the unit
c) Select the Port the units USB is connected to; in Sketch menu TOOLS → PORT
- To determine Port; Open Windows Device Manager Ports ( COM & LPT ) a new COM?? port appears right after plugging in the cable →
d) Select the Board; Sketch menu TOOLS → BOARD → ARDUINO/GENUINO UNO
e) In Arduino Sketch IDE; Press the Right-Arrow next to the Check mark in the Top-Left Corner to upload the firmware onto the unit
B. Virtual Pins
C. Customizing

✔ Overview
◌ Downloaded firmware includes menu items for;
- Pump Controller Selection | - Ability to control multiple Pump Controllers from one Hand-Remote Unit
- Power | - Sets or Read the Pump Power as either ON or OFF
- Water Level | - An Accessory IO-Monitor to check the canal or ditch water level
- Battery | - Reads the Battery Voltage Level
- Pressure | - An Accessory IO-Monitor to check the water pressure
- Alarms | - Various Alarms for the monitoring the readings above

The menu items are defined in the SetupMenu() Function identified by line 'void SetupMenu() {'. Each item in the Menu has a numeric index (i.e. Menu[index-#]).

/******************************************************************************************************************//**
* @brief Setup the LCD menu
* @remarks
* - Allows a single spot customization to users configuration
* @code
* exmaple code
* @endcode
**********************************************************************************************************************/ void SetupMenu() {

// Be sure to change 'MENUITEMS' when adding/deleting items
Menu[PUMPIDX].Text = "Pump";
Menu[PUMPIDX].ValueLocation = EPROM;
Menu[PUMPIDX].Option[0].Text = "Canal";
Menu[PUMPIDX].Option[0].TransceiverID = 10; | // Target TRANSCEIVER_ID
Menu[PUMPIDX].Option[1].Text = "Ditch";
Menu[PUMPIDX].Option[1].TransceiverID = 11; | // Target TRANSCEIVER_ID
Menu[PUMPIDX].LastOption = 1;
Menu[PUMPIDX].Poll=false; | // Poll for Updates
Menu[PUMPIDX].Val[SET].Active = true;

Menu[1].Text = "Power";
Menu[1].ValueLocation = REMOTEPIN_DIGITAL;
Menu[1].Option[0].Text = "Off"; Menu[1].Option[0].Value = LOW;

( 4.2 SYSTEM OPERATIONS :: Firmware :: Firmware ) Page -29-

Menu[1].Option[1].Text = "On"; Menu[1].Option[1].Value = HIGH;
Menu[1].LastOption = 1;
Menu[1].Pin = 7;
Menu[1].Val[SET].Active = true; | // Allows Value to be 'SET'
Menu[1].Val[LOALARM].ID = 'p';
Menu[1].Val[HIALARM].ID = 'P';

Menu[2].Text = "Water L.";
Menu[2].ValueLocation = REMOTEPIN_ANALOG; Menu[2].Pin = 64;
Menu[2].Val[LOALARM].ID = 'l'; Menu[2].Val[HIALARM].ID = 'L';

Menu[3].Text = "Battery";
Menu[3].ValueLocation = LOCALPIN_ANALOG; Menu[3].Pin = BATT_PIN; // Analog A2 Menu[3].Val[LOALARM].ID = 'b';

Menu[4].Text = "Pressure"; Menu[4].ValueLocation = REMOTEPIN_ANALOG; Menu[4].Pin = 3; // Analog A3 Menu[4].Val[LOALARM].ID='r'; Menu[4].Val[HIALARM].ID='R';

// Read all values at start-up
GetItem(PUMPIDX);
SetPump( Menu[PUMPIDX].Option[ Menu[PUMPIDX].Val[MAIN].Value ].TransceiverID ); idx = STARTIDX;
}
✔ To delete a Menu Item
◌ Find the menu items index (ie. Menu[index]) you'd like to delete by identifying it by its' Menu[Index].Text setting
◌ Select ALL Menu[index] lines with the same index
◌ Press delete
◌ Starting from the top make sure the indexes are in order; for example if you deleted [3], change [4] to [3], [5] to [4] and etc.. for all entries ◌ Up towards the top of the program ( ~line 50 ) change value of '#define MENUITEMS ?' to the number of menu items that exist now

✔ To add a Menu Item
◌ Start a new line below the last one defined and enter the attributes that need to be set
- Menu[?].Text | - The text that will display on the LCD
- Menu[?].Value | - Typically not set; holds the value of the item
- Menu[?].ValueSettable | - TRUE/FALSE determines if the user can change the value
- Menu[?].ValueLocation | - PROG/LOCALPIN/REMOTEPIN/EPROM; Determines where the value of the item is set/retrieved
- Menu[?].Pin | - Arduino Pin# associated with the item
- Menu[?].Analog | - TRUE/FALSE; Default is FALSE, Set to 'true' if using an Analog pin for the value
- Menu[?].AlarmCompare | - LESS/GREATER/EQUAL; Defines how an alarm will compare its limit value to the ValueIdx Value
- Menu[?].AlarmValueIdx | - The Menu[Index].Value this alarm item will compare itself with
- Menu[?].Option[?].Poll | - TRUE/FALSE; Default is true. Set to false if the value doesn't need to be refreshed and displayed

Options are how a limited amount of select-able items are defined for a value. For example ON or OFF would be two options.

- Menu[?].Option[?].LastOption - Counting from 0-> ; How many options are defined
- Menu[?].Option[?].Text | - Option[?].Text defines an option that can be selected like 'ON'
- Menu[?].Option[?].DrivePin | - Option[?].DrivePin LOW or HIGH when this option gets selected

◌ Up towards the top of the program ( ~line 50 ) change value of '#define MENUITEMS ?' to the number of menu items that exist now

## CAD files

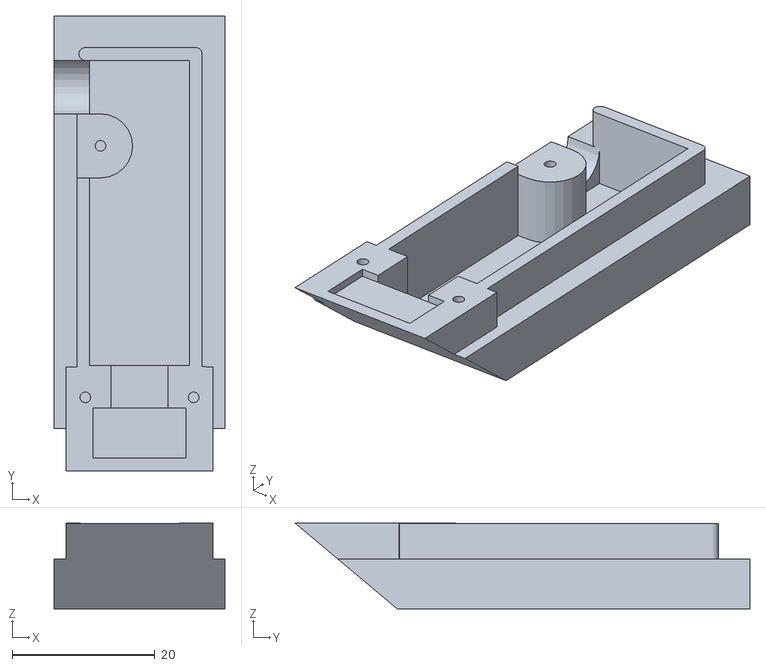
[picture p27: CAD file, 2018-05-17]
Accessories/Hydrometer/HydrometerCover.stl
24.0 x 63.8 x 12.0

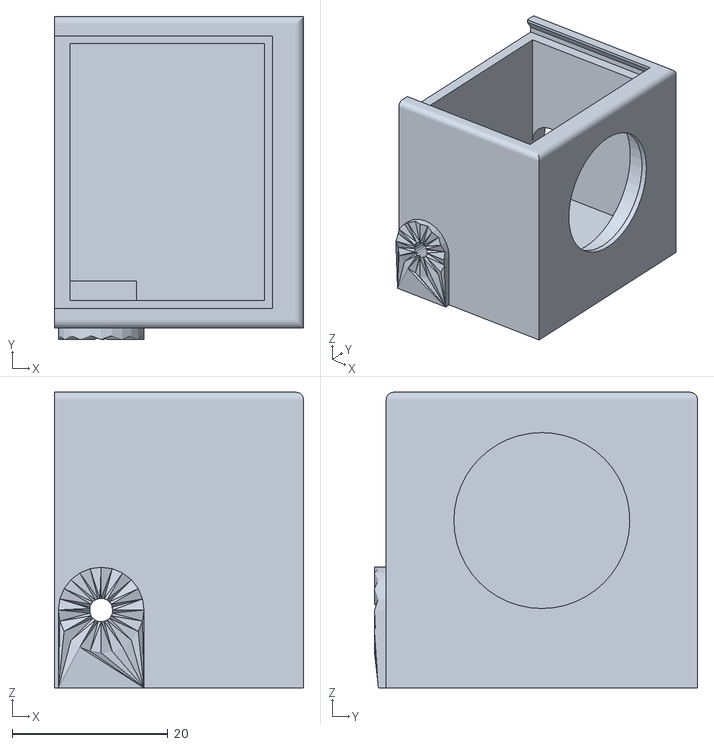
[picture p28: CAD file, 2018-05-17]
Accessories/Sonic Water Level Meter/3D-Prints-STL/SonicHeadCase.stl
32.0 x 41.5 x 38.0

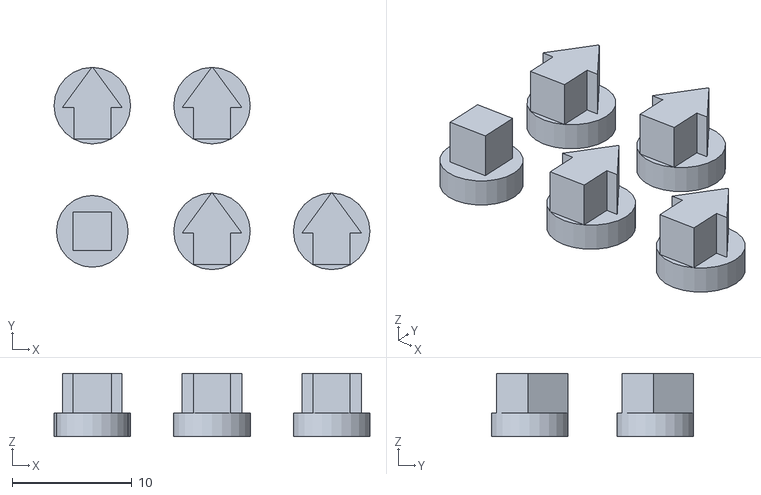
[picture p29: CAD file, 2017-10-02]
HandRemote/3D-Prints-STL/HandRemote-Buttons.stl
26.4 x 16.9 x 5.30

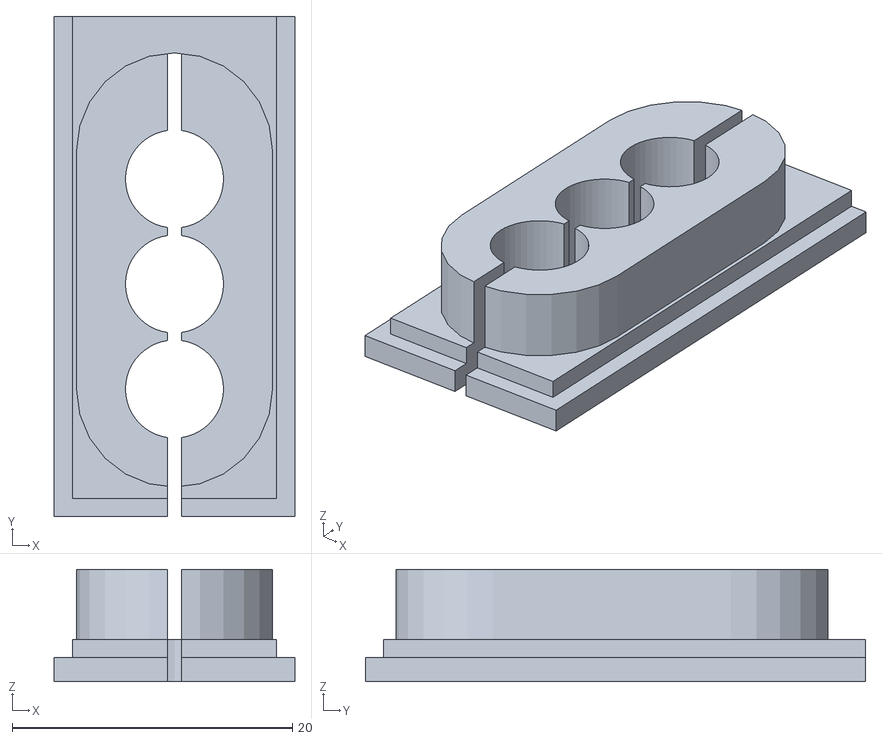
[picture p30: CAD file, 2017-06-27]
PumpController/3D-Prints-STL/PumpController-CableClampCover.stl
17.2 x 35.7 x 8.00

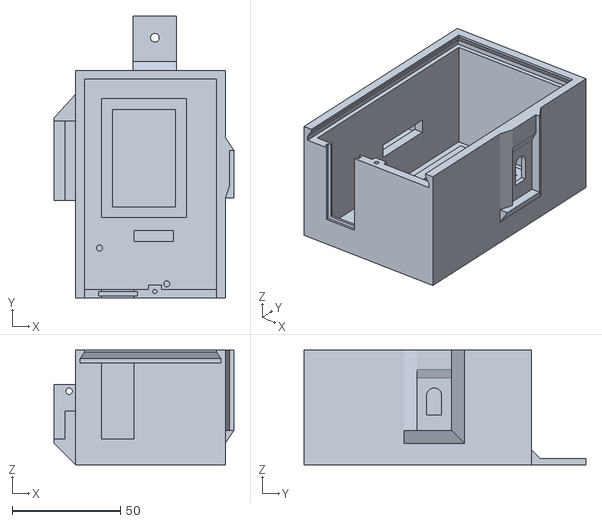
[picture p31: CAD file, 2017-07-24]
Sandbox/Pump-Controller-W-LCD/3D-Prints-STL/PumpController-Case.stl
83.0 x 130.0 x 53.0

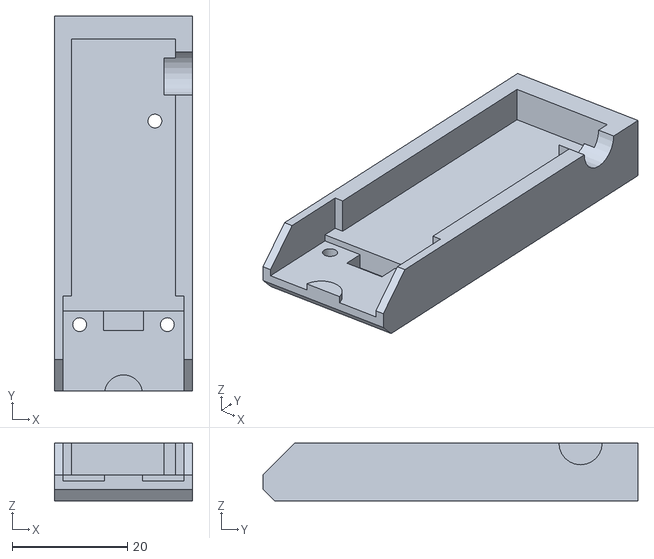
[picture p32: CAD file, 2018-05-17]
Accessories/Hydrometer/HydrometerCase.stl
24.0 x 65.0 x 10.0

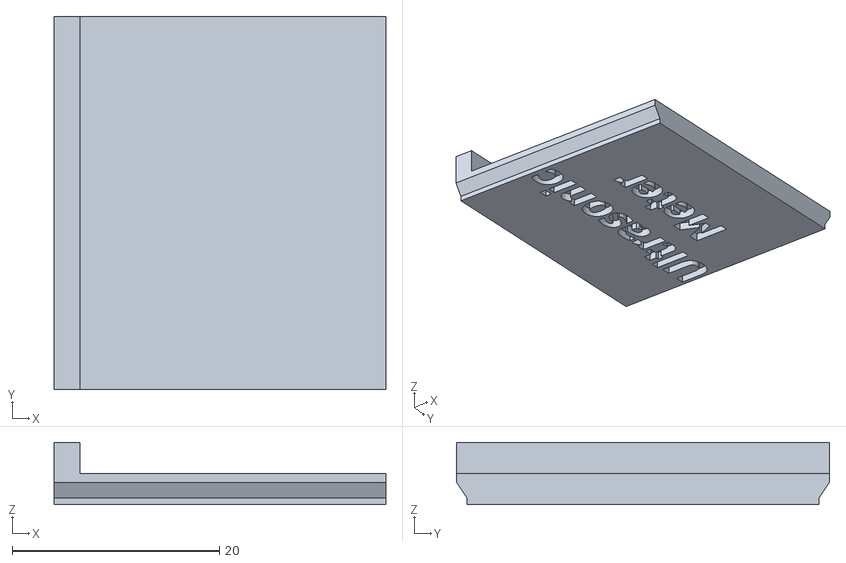
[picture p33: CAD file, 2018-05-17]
Accessories/Sonic Water Level Meter/3D-Prints-STL/SonicHeadCover.stl
32.0 x 36.0 x 6.00

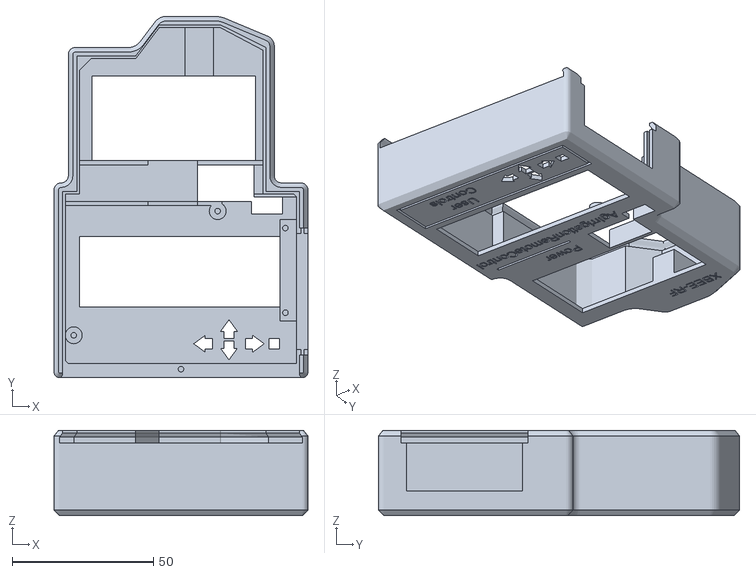
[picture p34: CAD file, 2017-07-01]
HandRemote/3D-Prints-STL/HandRemote-Case.stl
90.0 x 128.0 x 30.2

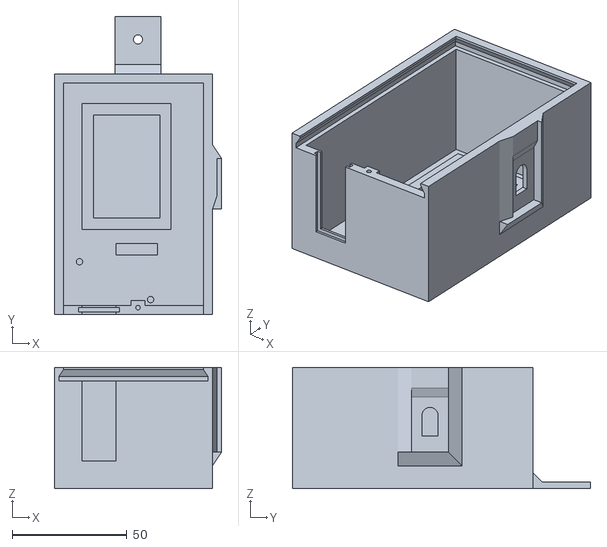
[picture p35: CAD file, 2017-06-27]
PumpController/3D-Prints-STL/PumpController-Case.stl
73.0 x 130.0 x 53.0

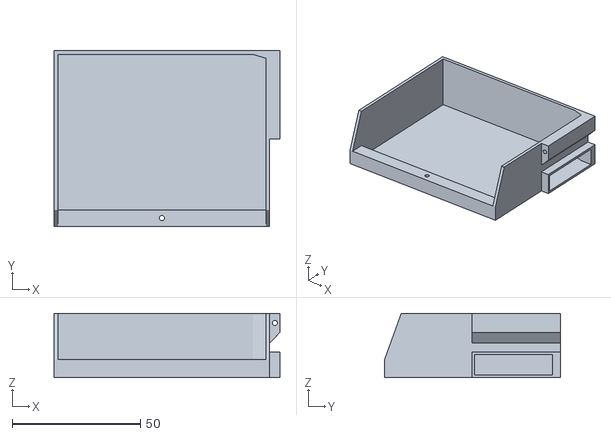
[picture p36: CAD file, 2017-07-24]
Sandbox/Pump-Controller-W-LCD/3D-Prints-STL/PumpController-LCDCase.stl
88.0 x 68.5 x 25.0

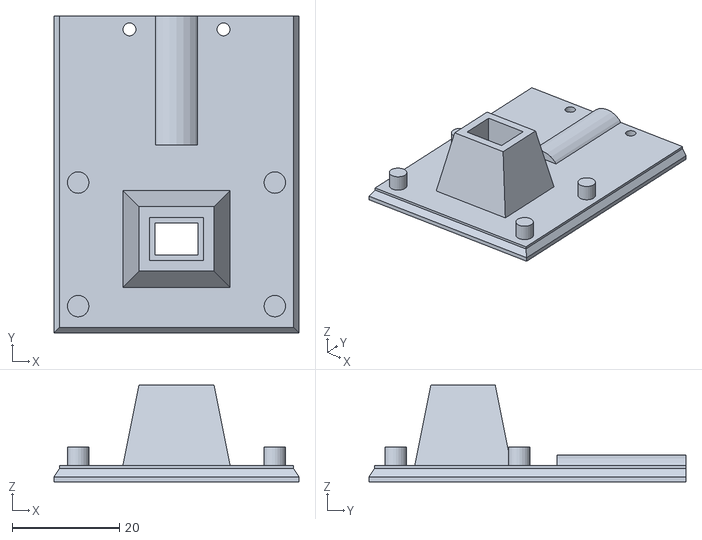
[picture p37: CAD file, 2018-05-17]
Accessories/Sonic Water Level Meter/3D-Prints-STL/SonicBoardCover.stl
45.6 x 59.0 x 18.0

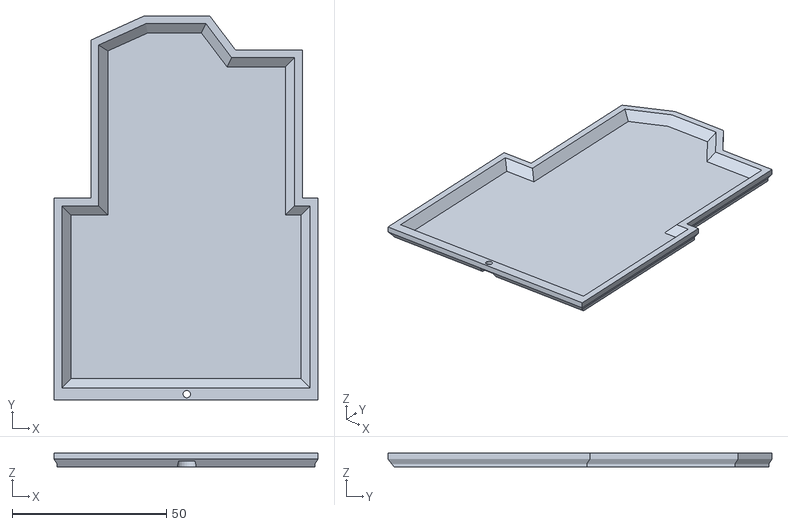
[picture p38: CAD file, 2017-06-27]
HandRemote/3D-Prints-STL/HandRemote-BackCover.stl
85.5 x 124.4 x 4.50

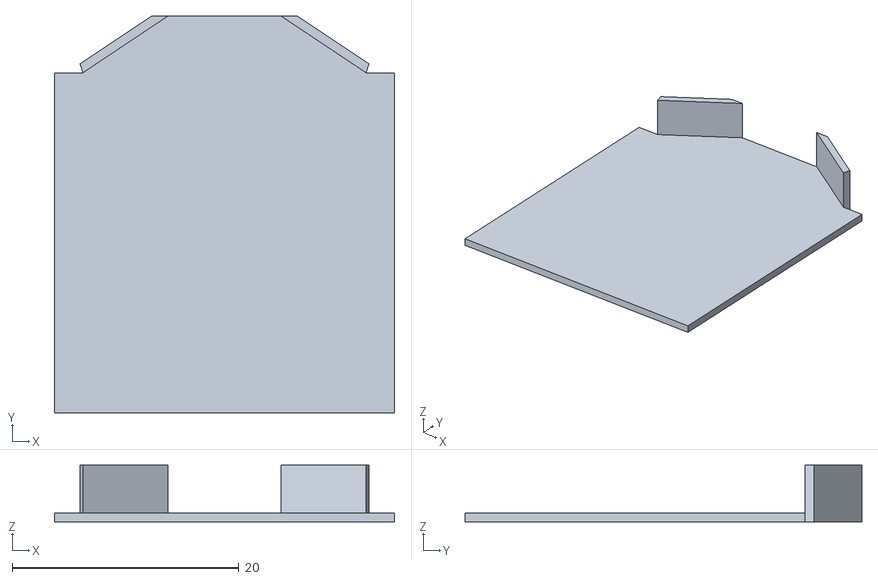
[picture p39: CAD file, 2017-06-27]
PumpController/3D-Prints-STL/PumpController-XbeeInsulatorPlate.stl
30.0 x 35.0 x 5.00

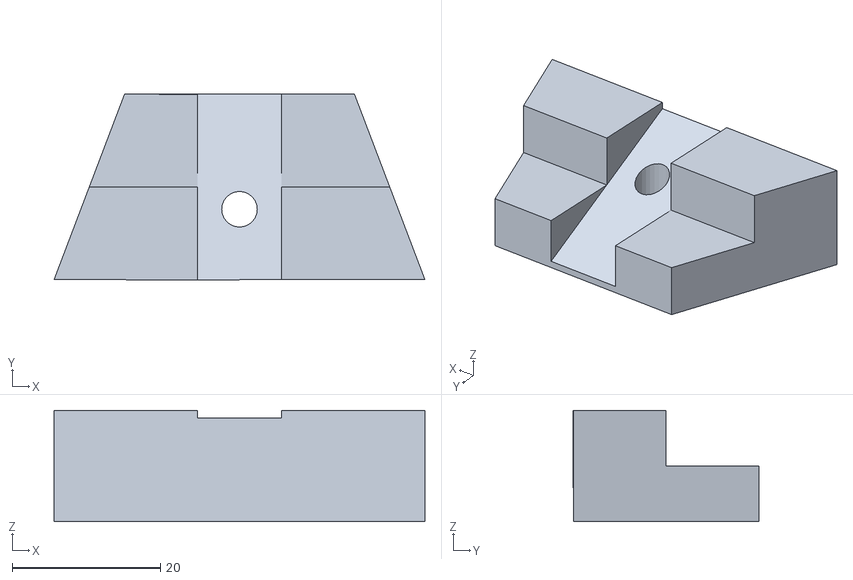
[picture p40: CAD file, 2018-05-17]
Accessories/Sonic Water Level Meter/3D-Prints-STL/Lever-Clamp.stl
50.0 x 25.0 x 15.0

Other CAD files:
HandRemote/3D-Prints-STL/HandRemote-BatteryInsulatorPlate.stl
PumpController/3D-Prints-STL/PumpController-Cover.stl
Accessories/Sonic Water Level Meter/3D-Prints-STL/SonicBoardCase.stl
HandRemote/3D-Prints-STL/HandRemote-BatteryCover.stl
Accessories/Hydrometer/HydrometerCase.skp
Accessories/Hydrometer/HydrometerCover.skp
Accessories/Sonic Water Level Meter/3D-Prints-STL/Lever.stl
Accessories/Sonic Water Level Meter/3D-Prints-SketchUp/Lever-Clamp.skp
Accessories/Sonic Water Level Meter/3D-Prints-SketchUp/Lever-Template.skp
Accessories/Sonic Water Level Meter/3D-Prints-SketchUp/Lever.skp
Accessories/Sonic Water Level Meter/3D-Prints-SketchUp/SonicBoardCase.skp
Accessories/Sonic Water Level Meter/3D-Prints-SketchUp/SonicBoardCover.skp
Accessories/Sonic Water Level Meter/3D-Prints-SketchUp/SonicHeadCase.skp
Accessories/Sonic Water Level Meter/3D-Prints-SketchUp/SonicHeadCover.skp
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

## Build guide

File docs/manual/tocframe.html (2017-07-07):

AgIrrigationPumpRemoteControl



AgIrrigationPumpRemoteControl.odt

Table of Contents

1. INTRODUCTION 2
A. Signal Strength ( 2-Miles ) 2
B. Features 3
2. INSTALLATION INSTRUCTIONS 3
A. Electrical Panel Introduction 4
B. DIN-Rail Mounting 5
C. Pump Panel wiring 6
D. Pump-Controller 7
E. Testing 7
3. OPERATING INSTRUCTIONS 8
A. Introduction 8
B. Display Table 9
C. Alarms 9
4. BUILDING INSTRUCTIONS 10
4.1 Bill Of Materials (BOM) = $233 10
A. Pump-Panel Components ( $91.50 ) 10
B. Electronic Control ( $29.17 ) 10
C. RF Electronics ( $91.32 ) 11
D. Wire & Connectors ( $30.72 ) 11
E. Tools Required ( $NA ) 12
4.2 Hand-Remote ( $69.58 ) 13
4.2.1 Electronics Assembly 13
A. LCD Keypad Shield 14
B. Zigbee/Xbee Shield 15
C. Active Buzzer 16
4.2.2 Hardware Assembly 18
A. 3D-Prints ( $2.82 ) 18
B. Install Electronics 18
C. Wire in Battery Power 19
4.3 Pump-Controller ( $82.05 ) 21
4.3.1 Electronics Assembly 21
A. 3D-Prints ( $0.20 ) 22
B. Perfboard Assembly 22
4.3.2 Hardware Assembly 25
A. 3D-Prints ( $3.87 ) 25
B. Install Electronics 26
C. Install Cable 27
4.4 Installation-Kit ( $98.07 ) 29
A. DIN Rail & Components 29
B. Pump-Panel Exit Cable 29
C. Miscellaneous Items 29
5. SYSTEM SETUP 30
5.1 Adding Expansions 30
5.2 Uploading Firmware 30
5.3 Xbee RF Configuration 31
5.4 Customizing Firmware 31
5.4.1 Pump-Controller 32
A. Virtual Pins 32
5.4.2 Hand-Remote 32
A. Adding & Deleting Devices 32
B. Creating a Menu-Item 33
C. Deleting a Menu-Item 33
D. Menu-Item Setup ( Example ) 33
6. OPTIONAL ACCESSORIES 36
6.1 Hand-Remote 36
6.1.1 9V Rechargeable Batteries ( $18.90 ) 36
6.2 Pump-Controller 36
6.2.1 Pressure 36
A. Materials ($9.59) 36
B. Installation 36
C. Firmware Adjustments 37
6.2.2 Water Level 37
A. Materials ( $10.77/ea ) 37
B. 3D-Prints ( $1.30 ) 37
C. Firmware Adjustments 38
6.2.3 Auxiliary Contact ( $43.75 ) 38
6.2.4 Flow Meter 38
7. TROUBLESHOOTING 38
8. OTHER RESOURCES / LINKS 39

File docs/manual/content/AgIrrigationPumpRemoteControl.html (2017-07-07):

( 7. TROUBLESHOOTING :: TROUBLESHOOTING :: TROUBLESHOOTING ) Page -39-

Ag Irrigation Remote Control

Using Arduino-UNO and Digi-Xbee RF


Written By: Thomas G (01/2017)

Feel free to use: no strings attached (text content only / images respectfully referenced)

Last Updated: 2017.06.30

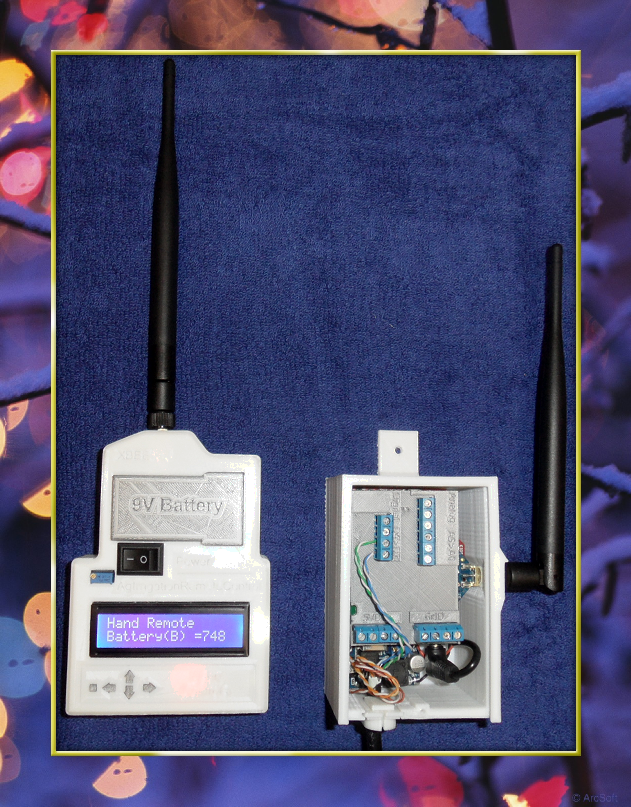
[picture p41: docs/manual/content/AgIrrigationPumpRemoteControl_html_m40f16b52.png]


# 1.INTRODUCTION

The “Ag Irrigation Remote Control” project's goal is to provide Radio Frequency (RF) remote control and monitoring abilities to an Agriculture-Industrial 3-Phase 480VAC Irrigation Pump that is typically used in wheel-line and hand-line irrigation setups within the United States.

- The project implements
  - Digi Xbee RF (https://www.digi.com/products/xbee-rf-solutions) radio modules ( S3B, 900MHz, 1/4-Watt ) which advertises a broadcast range of up to 28-miles ( Practical usage at 2-miles at ground level )
  - Arduino micro-controller boards, LCD display shields, Zigbee shields, and various discrete devices
- The project consists of:
  - Hand-Held “Hand Remote”
  - Pole mounted “Pump Controller”
  - High-Voltage Control “Installation Kit” which consists of components to be added to the pumps electrical panel
- The project is Open Source and its main page Resides at: https://github.com/tgit23/AgIrrigationRemoteControl
  - Releases ( All Finalized Plans, Files and Documentation ) can be downloaded at: https://github.com/tgit23/AgIrrigationRemoteControl/releases
  - This document ( most recent version ) can be seen at: https://tgit23.github.io/AgIrrigationRemoteControl/AgIrrigationPumpRemoteControl.pdf
  - Pre-Built Purchasing options are available – See the projects main page link above

#### A.Signal Strength ( 2-Miles )

- Standard Signal distance is recommended for usage of up to 2-miles
  - Elevated or higher gain antennas can be purchased to extend this range
  - Test Scenario
    - Pump-Controller mounted 5-feet from the ground on the power pole next to the pump
    - Hand-Controller checked inside a moving vehicle ( ~ 3-feet off the ground )
  - Test Environment
    - Houses located on square mile blocks; each mile having approximately 6 to 10 houses per mile
    - Ground level is fairly flat
  - Results
    - < 1-mile - Coverage approximately 99% of spot locations ( very few spots inside a house will loose signal )
    - 1-to-2 miles - Coverage approximately 90% of spot locations ( a few spots inside a vehicle will loose signal )
    - 2-to-3 miles - Coverage approximately 5% of spot locations ( very few spots get a signal )
    - 3-to-4 miles - A few signals were obtained at up to 3-3/4 miles away; but spot location was very very temperamental.

#### B.Features

- A solid rural 2-Mile range
- No cellular, FCC licensing or other requirements are needed; Just hook it up and use it
- A single Hand-Remote can control multiple irrigation pumps
- Multiple Hand-Remotes can control the same irrigation pump
- Uses the Pump Panels “AUTO” selection; so it doesn't disturb manual operation of Hand-Off & Start sequences
- Implements a “Stay-Off” after power losses that is required by power companies
- Easily expandable to offer Pressure and Water-Level monitoring
- Built upon mass-produced development boards that can be easily purchased and replaced
- Hand-Remote settable Alarms ( buzzer ) to notify user of
  - Power changes - For Example; Alarms when pump shuts down due to a power loss
  - Water Pressure boundaries ( if equipped ) - For Example; Alarms when pressure drops due to a hose that has fallen off or broken pipe
  - Ditch Water-Level boundaries ( if equipped ) - For Example; Alarms when water in the ditch is too low or too high

# 2.INSTALLATION INSTRUCTIONS

This section is a guide to installing the Pump-Controller using the Installation Kit. If these products were not purchased they can be built by following the #4.BUILDING INSTRUCTIONS|outline listed in this document.

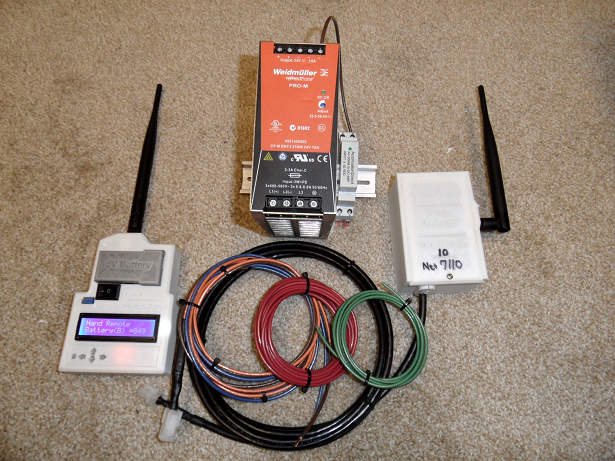
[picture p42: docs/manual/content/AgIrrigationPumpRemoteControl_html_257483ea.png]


Installation will require the following SUPPLIES

Pump-Controller

The white box shown on the right in the picture above
Including the attached Antenna, Cable and 4-pin plug ending

Installation Kit ( Including the following items )

A 3-Phase Power Supply attached to a DIN rail

480VAC Input to 24Vdc Output

A Solid State Relay (SSR) attached to a DIN rail

480VAC ( or higher ) Load Voltage and 5Vdc Input

12-feet of RED 600V 16-Gauge or heavier THHN or MTW wire
4-feet of GREEN 600V 16-Gauge or heavier THHN or MTW wire
A Pump-Panel Exit Cable

A 4-pin plug ending attached to (3) 4ft 600V rated wires

Yellow plug wire → Orange Hookup wire (+Vdc)
Black plug wire → Brown Hookup wire (-Vdc)
White plug wire → Blue Hookup wire (SSR-Control)
Green plug wire → Unused ( None )

(2) #8-32 x 1/2” Machine Screws
(1) Wood screw for mounting the Pump-Controller to a pole

Installation will require the following TOOLS

Personal protective gear ( e.g. insulated/flash protection clothing )
Voltmeter - that reads up to or beyond 500VAC
Cordless drill
Wire strippers and cutters
#1 Phillips and #1 Flat head screw drivers
Center Punch
#29 ( 9/64” ) Drill Bit
#8-32 Threading tap

#### A.Electrical Panel Introduction

Read through the following section to gain general knowledge on the items within the pumps electrical panel.

Most 3-phase irrigation pumps that do not have variable frequency drives(VFD) or inverters are setup similarly. Below is the details of a pumps electrical panels as an example or reference to the pumps power circuit. This information was gathered to determine the wiring and power needed to control the pumps power.

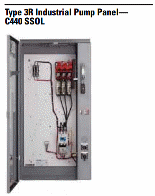
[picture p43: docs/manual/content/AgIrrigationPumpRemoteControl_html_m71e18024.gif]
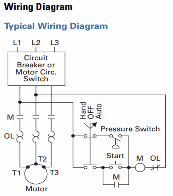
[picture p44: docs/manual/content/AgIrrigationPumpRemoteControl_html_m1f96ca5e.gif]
 

- Wiring Diagram Description
  - L1, L2, L3 - Are the three HOT wires of the 3-Phase Power ( 480VAC ) going through the main breaker
  - M - The Starter Contactor ( example picture below ) contains:
    - Activation Coil - Represented by the M-Circle in the wiring diagram just right of the Start Button ( this Activates the “Hammer” Switch )
      - The Activation Coil resides “inside” the “Starter Contactor” Assembly; but can be removed by disassembling the unit.
    - Main Contacts - The M-Contacts (-||-) that connects the L1,L2,L3 lines → OL ( Overloads ) → Motor ( Sometimes called the “Hammer” )
      - The Main Contacts are significant part of the “Starter Contactor” as a whole unit.

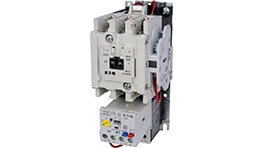
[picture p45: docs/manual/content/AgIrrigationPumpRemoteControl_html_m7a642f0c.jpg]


    - Hold Contact - Represented by the M-Contact (-||-) wired in parallel and just below the Start Button
      - The Hold Contact “LOCKS” the Activation coil ON when the Start-Button is pressed.
      - The Hold ( sometimes referred to as an Auxiliary Contact ) clamps onto the side of the “Starter Contactor”
      - As shown in picture above as the clamped on the right unit with a Grey square center.
  - Hand, Off, Auto Switch
    - In the wiring diagram above; the Hand-Off-Auto selector switch is in the “Auto” position where it is then connected to a Pressure Switch
    - The Solid State Relay, that is part of the Installation kit, will be attached where this “Pressure Switch” is shown in the diagram.

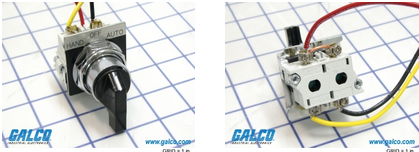
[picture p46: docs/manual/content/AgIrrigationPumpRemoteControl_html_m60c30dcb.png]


- Description of Operation

When HAND is selected the “control circuit” ( L1 → L2 loop ) is still open until the Start Button is pressed. When the Start button is pressed it activates the (M) Activation Coil which in-turn activates the “Hold Contact” ( the --| |-- in parallel to the Start Button). This right-side contactor holds the “control circuit” closed until there is a power failure bump or the Hand-Off-Auto Switch breaks open the circuit loading the (M) activation coil.

This Projects SSR-Relay will be connected where the “Pressure Switch” is shown in this wiring diagram and will use the AUTO switch selection. This setup will require that the Arduino NOT re-activate power after a power failure has occurred until a specified time delay or turned back on. The click in HAND circuit is setup so the power company can re-activate power after a power failure without the over-load of all motors kicking on at the same time.

- Checking Amperage Limitations
  - Activation Coil Amperage can be gotten by looking up the “Starter Contactor” specification sheet, for example;
    - See Page 9 “AC COIL DATA” for NEMA Size #2 Shows 230VA(Volt-amperes which is VA=V*A) so 230VA/480Vac = 0.479Amps @ 480V
    - The Solid State Relay in the Installation Kit can supply up to 10A; So it is well equipped to handle much larger Starter Contractors.
- Links to more information
  - http://www.eaton.com/ecm/idcplgIdcService=GET_FILE&allowInterrupt=1&RevisionSelectionMethod=LatestReleased&noSaveAs=0&Rendition=Primary&dDocName=998056282226
  - http://www.eaton.com/Eaton/ProductsServices/Electrical/ProductsandServices/AutomationandControl/EnclosedControl/NEMA/PumpPanels/index.htm

#### B.DIN-Rail Mounting

BE SURE THE MAIN BREAKER IS TURNED OFF AND CAREFULLY CHECK THAT THERE IS NO VOLTAGE ON THE OUTPUT OF THE MAIN BREAKER WITH A PROPER METER!!! 480VAC is deadly; and can cause severe flash burn and/or death. (e.g. A meter on the wrong setting can “flash” explode causing “flash” burns on you even at a distance away). I DISCLAIM ANY AND ALL RESPONSIBLITY FOR ANY RISKS, HARMS, INJURIES OR PROPERTY DAMAGE THAT WAS A RESULT OF FOLLOWING ANY INSTRUCTION IN THIS MANUAL.

See https://www.youtube.com/watch?v=6hpE5LYj-CY

1. Check your volt meter
  a. Before leaving to install; check that your volt meter is working by plugging it into a household outlet ( Use the same setting >500 VAC )
  b. Make sure the probes are plugged into their correct spots on the meter
  c. Do not make any more changes to the volt meter after testing its correct operation.
2. Follow safe practices
  a. Never turn ON the main breaker with the panel open
  b. Never stand in front of the panel while turning on the main breaker ( flash explodes will often blow the front panel clear off ) - stand at the side
  c. Never work in the same side of the box where the live wires ( feed wires ) exist – generally at the top of the box
  d. Always stand as far away as you can
3. Prepare for Installation
  a. Switch the Main Breaker to OFF from the outside of the pumps electrical panel
  b. Open the pumps electrical panel
  c. Double check your voltmeter setting – Never measure for 480VAC with a lower setting; it will cause many meters to flash explode
  d. With leather gloves on, very carefully making sure not to wiggle the probes out of place, measure the following voltages
    - From the bottom of the Main Breaker; Measure voltage between each of the 3-connectors ( They should all be 0V)
    - From the bottom of the Main Breaker; Measure voltage between each of the 3-connectors and the ground metal of the electrical panel ( 0V )
4. Plan a location inside the Electrical Panel for the Power Supply and SSR mounted on the DIN rail
  a. Requires approximately a 6” Wide x 6” Tall x 6 1/2” Deep envelope
  b. Find a location as far away from other hot wires as possible ( eliminate the risk of a loosened wires falling and touching a low-voltage wire )
  a. Preferably a location at the bottom of the box where the exit plug can quickly drop out of the box.
5. Mount the DIN Rail
  a. Hold the DIN Rail in the desired location and punch the metal through easily accessible mounting slots in the DIN Rail on both ends
  b. Drill two holes in the punch markings ( Bit Size #29 – 9/64” - 0.1360” )
  c. Tap-thread the two holes just drilled ( #8-32 threading tap )
  d. Hold the DIN rail in place and fasten it with (2) #8-32 machine screws
6. Attach ( If taken off ) the Power Supply and Solid State Relay to the DIN Rail

#### C.Pump Panel wiring

NOTICE: All wiring in this section should be done with 600V rated wire

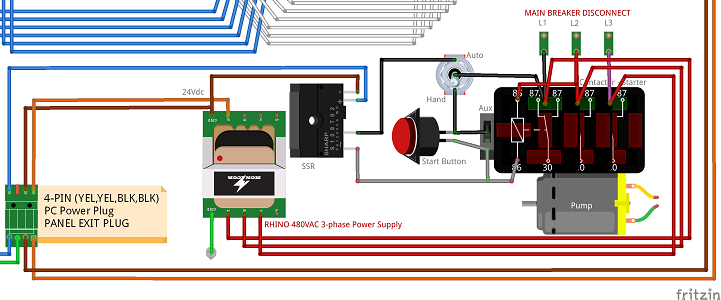
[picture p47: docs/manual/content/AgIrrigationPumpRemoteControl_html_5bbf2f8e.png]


1. Wire the 480VAC 3-Phase Power Supply attached to the DIN Rail
  a. Using RED wire; connect Power Supply Terminals L1, L2, L3 to the top terminals of the Contactor ( i.e. Starter / Hammer ) L1, L2, L3 terminals
    - Often this is easiest to do by wiring to a “Motor Saver” unit that is already wired to L1, L2, L3 if your panel has one
  b. Using GREEN wire; connect Power Supply Ground (ꔍ) to a bolt or terminal connected to the panels back-plane
2. Wire the Solid State Relay attached to the DIN Rail
  a. Using RED wire; connect Solid State Relay (15) → AUTO Terminal of the HAND-OFF-AUTO switch ( Typically the only unused terminal )
  b. Using RED wire; connect Solid State Relay (16) → OPPOSITE side of the start button as the wire from the HAND-OFF-AUTO to the Start Button
3. Wire in the Pump-Panel Exit Plug
  a. With the Plug end of the Exit Plug outside the box; insert the wires through a bottom hole in the Pumps Electrical Panel
  b. Connect the
    - Orange wire → 24Vdc(+) of the Power Supply
    - Brown wire → 24Vdc(-) of the Power Supply
    - Blue wire → (A1)+ of the Solid State Relay
  c. Verify that a BROWN wire already exists from 24Vdc(-) of the Power Supply → (A2)- of the Solid State Relay

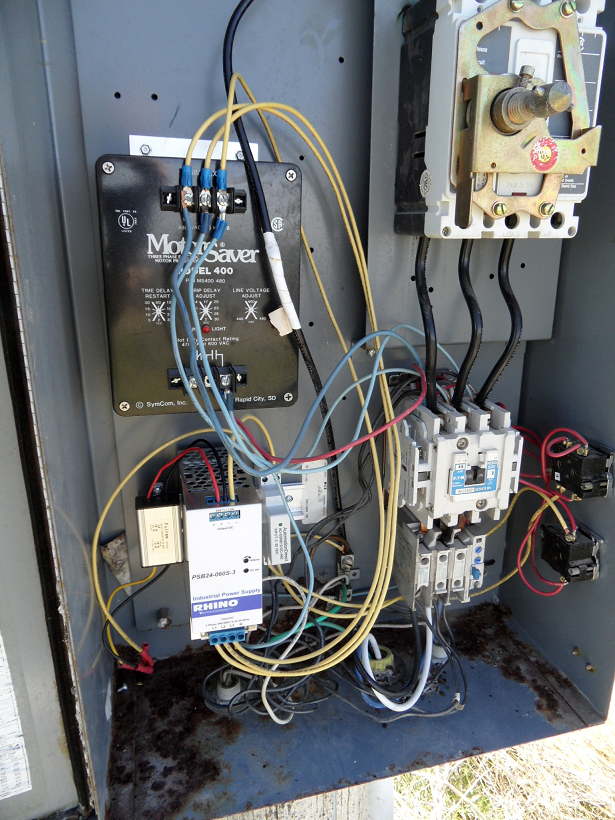
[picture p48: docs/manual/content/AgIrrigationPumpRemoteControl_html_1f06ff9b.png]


4. Close the Electrical Panel – Panel Control installation is now complete
  a. Wait until after installing the Pump-Controller before turning the breaker back on.

#### D.Pump-Controller

1. Plug the Pump-Controller into the Exit Plug installed in the steps above.
2. Attach the Pump-Controller box to the power pole using a wood screw at the desired height up the pole.

#### E.Testing

1. Turn the Electrical Panel Breaker ON.
2. Switch the Hand-Off-Auto switch to AUTO.
3. Using the Hand-Remote Device
  a. Find the Menu-Item “Power” for the Pump-Controller Device just installed
  b. Press (→ ) to 'SET->' and then UP/DOWN to set to ON
  c. Press the square 'Enter' button – The pump should start running
  d. While still on the “Power” Menu-Item; Press (→ ) till 'SET->' and then UP/DOWN to set to OFF
  e. Press the square 'Enter' button – The pump should shut off

# 3.OPERATING INSTRUCTIONS

#### A.Introduction

The Hand-Remote display has a Top Row and a Bottom Row

- Top Row ( i.e. The Status Row – not changed directly )
  - On the Left - The Device ( Unit ) that is currently under control or being monitored
  - On the Right - The Alarms currently active ( Alarm 'ID'entifying letters )
- Bottom Row ( i.e. The Control Row – changes are made directly on this row )
  - On the Left - The current Menu-Item ( Up-Down Arrows Change Item )
  - In the Middle - The current Action/Function to be applied to the Menu-Item ( Right-Left Arrows Change the Function )
    - If it is (=) - Function; Read Value for the current Menu-Item ( This can also be thought of as the “Main Menu” )
    - If it is (SET→) - Function; Set a New Value for the current Menu-Item
    - If it is (<!) - Function; Low Alarm value; A “too-low” numerical value that will trigger an alarm
    - If it is (=!) - Function; Low Alarm option; A “is-equal-to” option that will trigger an alarm
    - If it is (>!) - Function; High Alarm value; A “too-high” numerical value that will trigger an alarm
    - If it is (ǂ!) - Function; High Alarm option; A “not-equal-to” option that will trigger an alarm
  - On the Right - The function Value ( of or for ) the Device ( Up-Down Arrows Change the SET and/or ALARM VALUES )

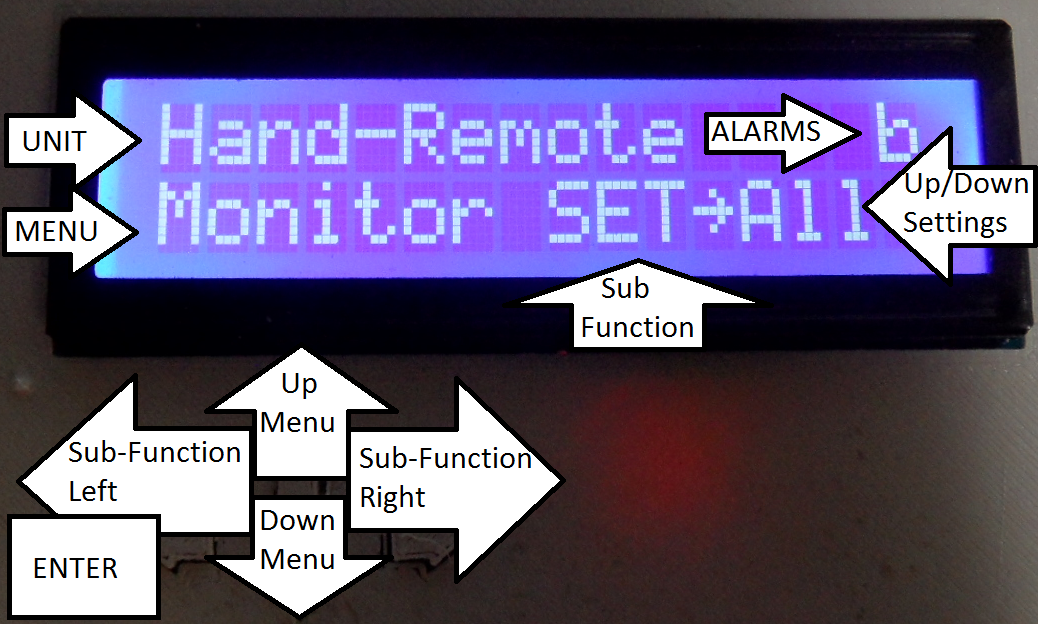
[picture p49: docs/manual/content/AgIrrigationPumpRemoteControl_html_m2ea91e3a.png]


#### B.Display Table

- Maneuvering the display items can be represented as a table like the one shown below
  - The “Location” Column is NOT part of the Display Menu; It shows where the item is wired to the Pump-Controller Hardware ( if applicable )
  - Disabled items are Skipped when maneuvering through the display table

| | SUB-FUNCTIONS ( ← LEFT || RIGHT → ) | | | | Location
| Device | MENU ITEMS (=) Up/Down Items ENTER to refresh | SET (→) Up/Down Changes ENTER to Apply | LOW ALARM (=!) (<!) Up/Down Changes ENTER Toggles On-Off | HI ALARM (ǂ!) (>!) Up/Down Changes ENTER Toggles On-Off | Wire to PIN ( NOT for Display )
Menu-Items ( ← UP || DOWN → ) | Hand-Remote | Battery(B) | DISABLED | (<!) When less than | (>!) When greater than | A1
| Ditch Pump | Power(P) | (SET→) On (SET→) Off | (=!) Equals “On” (=!) Equals “Off” | (ǂ!) Not Equal “On” (ǂ!) Not Equal “Off” | D7
| Ditch Pump | Water (L) | DISABLED | (<!) When less than | (>!) When greater than | V64(Trig=D4,Echo=D5)
| Ditch Pump | Pressure(R) | DISABLED | (<!) When less than | (>!) When greater than | A3
| Canal Pump | Power(P) | (SET→) On (SET→) Off | (=!) Equals “On” (=!) Equals “Off” | (ǂ!) Not Equal “On” (ǂ!) Not Equal “Off” | D7
| Canal Pump | Pressure(R) | DISABLED | (<!) When less than | (>!) When greater than | A3
| Canal Pump | Pressure(S) | DISABLED | (<!) When less than | (>!) When greater than | A4

* Note: V64 is Virtual Pin #64; Virtual Pins are memory spaces inside the Pump-Controller and therefore the Pump-Controller firmware actually identifies the connecting pins. This is used when Pump-Controller processing is done before a legitimate value can be determined.

#### C.Alarms

- Alarms check read/monitored values against desired values ( Low / High boundaries ) and notifies the user ( buzzing ) if boundaries are violated
  - Some menu items will have alarms while others will not – this is configured in the firmware and should be on a use-case scenario
  - Anytime a button is pressed an active alarm ( buzzing ) will quite until “idle-monitoring” is started again ( No button press for 30-seconds )
  - To permanently shut off the active alarm ( buzzing ) the alarm itself must be turned 'OFF'
- Alarms can be either turned ON or OFF
  - ON alarms are identified by the single character in the Top-Right of the Display
  - Alarms are switched from ON → OFF or OFF → ON by
    - Press UP/DOWN until the Menu Item you'd like to turn an Alarm On/Off for - is selected
    - Press RIGHT button to select which alarm to turn On/Off; Either the Low Alarm ( !=, !< ) or the High Alarm ( ! ǂ, !> )
    - Press ENTER button to Toggle the Alarm On/Off ( An On-Alarm goes Off; An Off-Alarms goes On )
- To Set an alarm value
  - Press UP/DOWN until the Menu Item you'd like to set an alarm boundary for is selected
  - Press the RIGHT button as many times as it takes to see one of the following indicators in the Middle of the Bottom Row
    - ( =! ) - Sound an alarm if the value becomes EQUAL to the one indicated
    - ( ǂ! ) - Sound an alarm if the value does NOT-EQUAL equal the one indicated
    - ( <! ) - Sound an alarm if the value becomes LESS-THAN the one indicated
    - ( >! ) - Sound an alarm if the value becomes GREATER-THAN the one indicated
  - Use the UP/DOWN buttons to select the comparison value or option
    - For Numerical values; Holding the UP/DOWN button for more than 5 counts will increase or decrease the value by 10
  - Press ENTER button to apply the selected comparison value ( Note; Applying a value will also Toggle the On/Off status of the Alarm )
- Notes
  - When the Hand-Remote looses signal the alarms are shut-off automatically until signal is restored
  - The Battery alarm will disable at any reading under 550. This prevents the battery from alarming while being powered by USB.

# 4.BUILDING INSTRUCTIONS

This section shows how the Hand-Remote, Pump-Controller and Installation Kit are built. It can be used to build your own setup by purchasing the individual pieces and assembling them yourself. It can also be used for troubleshooting problems or issues that may arise.

## 4.1Bill Of Materials (BOM) = $233

For a per device itemized listing see #4.2.Hand-Remote ( $69.58 )|outline, #4.3.Pump-Controller ( $82.05 )|outline or #4.4.Installation-Kit ( $98.07 )|outline

Note: The itemized prices include the PLA plastic filament costs for 3D-Printing and thus adds up to $249.70 instead of $233.

#### A.Pump-Panel Components ( $91.50 )

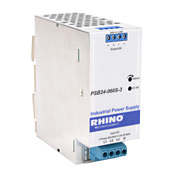
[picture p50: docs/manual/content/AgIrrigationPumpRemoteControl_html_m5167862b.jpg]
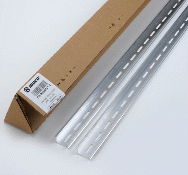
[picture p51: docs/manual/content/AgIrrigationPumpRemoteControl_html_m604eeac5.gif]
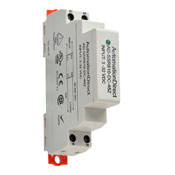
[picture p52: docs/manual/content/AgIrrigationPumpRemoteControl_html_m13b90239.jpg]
 (1) RHINO switching Power supply 320-600 VAC input, 3-phase 24 VDC output, 60W, 2.5A 35mm DIN Rail mountable AutomationDirect.com (https://www.automationdirect.com/adc/Shopping/Catalog/Power_Products_(Electrical)/DC_Power_Supplies/24VDC,_3-Phase_Input/PSB24-060S-3) ( $59.00/ea ) |  6” of DIN rail Slotted, 35mm, 10 mm height For mounting Power Supply and SSR of each Pump AutomationDirect.com (https://www.automationdirect.com/adc/Shopping/Catalog/Enclosures_-z-_Subpanels_-z-_Thermal_Management_-z-_Lighting/Enclosure_Subpanels_-a-_Internal_Mounting_A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) ( $8.00/2x 1-Meter Pieces ) |  (1) Solid state relay 3-32 VDC input 480VAC or higher SPST, N.O., SCR, 10A 35mm DIN-rail, Random type AutomationDirect.com (https://www.automationdirect.com/adc/Shopping/Catalog/Relays_-z-_Timers/Solid_State_Relays/DIN_Mount_Relays_(AD-SSR8_-z-_AD-SSR2_-z-_AD-SSR6_-z-_AD-HSSR8_Seri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) ( $24.50/EA )

#### B.Electronic Control ( $29.17 )

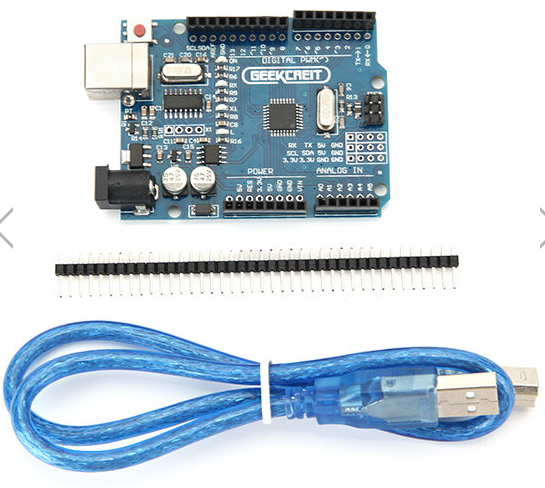
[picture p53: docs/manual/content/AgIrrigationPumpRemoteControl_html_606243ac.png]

(2) UNO R3 Atmega328P Development Board with Male Pin Header and USB Cable

AliExpress.com (https://www.aliexpress.com/item/Free-shipping-high-quality-UNO-R3-MEGA328P-CH340-CH340G-for-Arduino-UNO-R3-USB-CABLE/32353698284.html) ( $3.80/EA )
(1) for each HandRemote
(1) for each PumpController

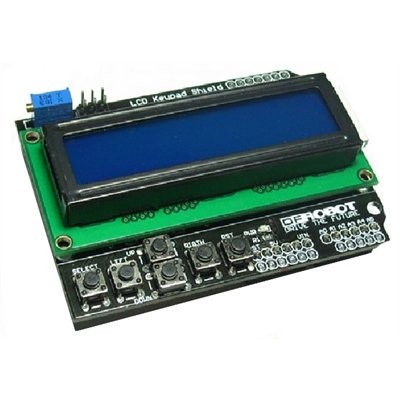
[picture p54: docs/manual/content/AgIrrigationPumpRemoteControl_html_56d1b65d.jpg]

(1) Keypad Shield Blue Back-light for
Arduino Robot LCD 1602 Board

AliExpress.com (https://www.aliexpress.com/item/Free-Shipping1PCS-LCD-Keypad-Shield-LCD1602-LCD-1602-Module-Display-for-arduino-ATMEGA328-ATMEGA2560-raspberry-NO/32787414048.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) ( $2.19/EA )
(1) Display for each HandRemote
Wiki (https://www.dfrobot.com/wiki/index.php/Arduino_LCD_KeyPad_Shield_(SKU:_DFR0009)
Schematic (http://image.dfrobot.com/image/data/DFR0009/LCDKeypad%20Shield%20V1.0%20SCH.pdf)
Layout (https://raw.githubusercontent.com/Arduinolibrary/DFRobot_LCD_keypad/master/DFR0009_Layout.png)

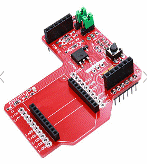
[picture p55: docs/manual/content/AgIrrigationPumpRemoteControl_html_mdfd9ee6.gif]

(2) Zigbee Shield RF Wireless Module
Expansion Board for Arduino Xbee

Aliexpress.com (https://www.aliexpress.com/item/XBee-Zigbee-Shield-RF-module-wireless-expansion-board/32801452766.html) ( $2.20/EA )
(1) for each HandRemote
(1) for each PumpController
Schematic (https://www.arduino.cc/en/uploads/Main/XbeeShieldSchematic.pdf)
Tutorial (https://www.cooking-hacks.com/documentation/tutorials/xbee-arduino-raspberry-pi-tutorial/)
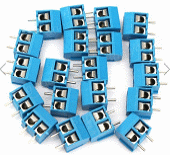
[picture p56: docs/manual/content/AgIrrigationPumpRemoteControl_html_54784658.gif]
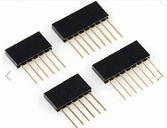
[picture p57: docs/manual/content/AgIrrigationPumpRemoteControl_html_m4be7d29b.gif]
 (15) 2x Pin Plug-in Screw Terminal Block Connector 5.08mm Pitch External I/O connections Banggood.com (http://www.banggood.com/20pcs-2-Pin-Plug-in-Screw-Terminal-Block-Connector-5_08mm-Pitch-p-993197.html) ( $2.15 / 20pcs ) (15) for each PumpController |  (1) 2-PIN Male – Zigbee → Perfboard POWER (1) 4-PIN Female – Perfboard → Zigbee POWER (2) 6-PIN Male – Zigbee I/O → Perfboard (1) 4-PIN Female - Zigbee->Perfboard RX/TX Aliexpress.com (https://www.aliexpress.com/item/10-pcs-4P-4pin-Female-Single-Row-Straight-Header-Strip-Socket-Connector-Pitch-2-54mm/32442087495.html) ( $0.79 / 10pcs ) (2) Female, (2) Male for each PumpController * Male Headers are part of Arduino Purchase * |  (1) Black Snap-in On/Off Rocker Switch Aliexpress.com (https://www.aliexpress.com/item/New-Black-Push-Button-Mini-Switch-6A-10A-110V-250V-KCD1-2Pin-Snap-in-On-Off/32670615106.html) ( $0.86 / 5pcs ) (1) for each HandRemote
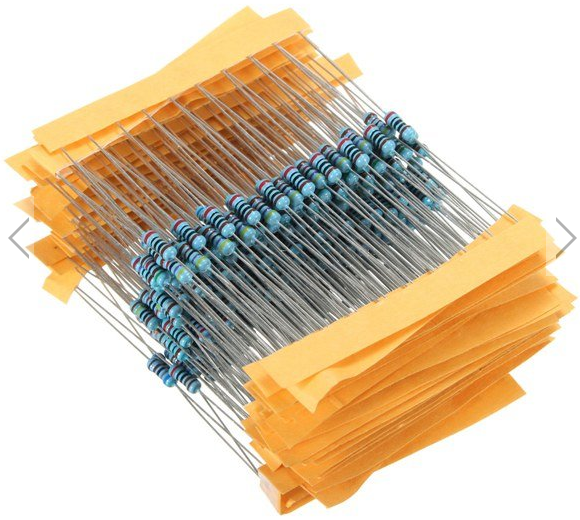
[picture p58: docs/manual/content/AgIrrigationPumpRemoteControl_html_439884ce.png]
 (1) Active Speaker Buzzer Alarm Aliexpress.com (https://www.aliexpress.com/item/KEYES-KY-012-Active-Buzzer-Module-FOR-The-ARDUINO-AVR-PIC/32740686896.html) ( $0.60 / ea ) (1) for each HandRemote |  (1) FR-4 Double Side 50cm x 70cm Prototype PCB Printed Circuit Board Aliexpress.com (https://www.aliexpress.com/item/Free-Shipping-4pcs-5x7-4x6-3x7-2x8-cm-double-Side-Copper-prototype-pcb-Universal-Board-for/32730636287.html) ( $1.56/ 4pcs ) (1) for each PumpController |  (2) Resistors 1 valued at 1/3 the other ( 10K-Ohms or higher ) Banggood.com (http://www.banggood.com/300Pcs-1-14W-Metal-Film-Resistor-Resistance-30-Values-Assortment-Kit-p-1091920.html) ( $2.28 / 300pcs ) (2) for each HandRemote
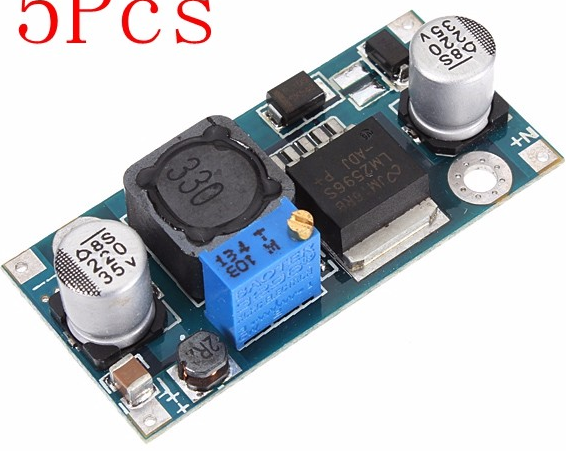
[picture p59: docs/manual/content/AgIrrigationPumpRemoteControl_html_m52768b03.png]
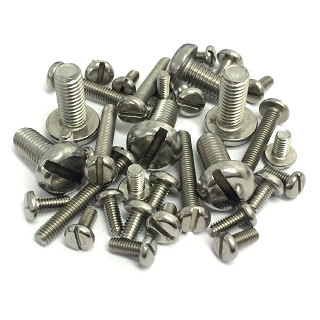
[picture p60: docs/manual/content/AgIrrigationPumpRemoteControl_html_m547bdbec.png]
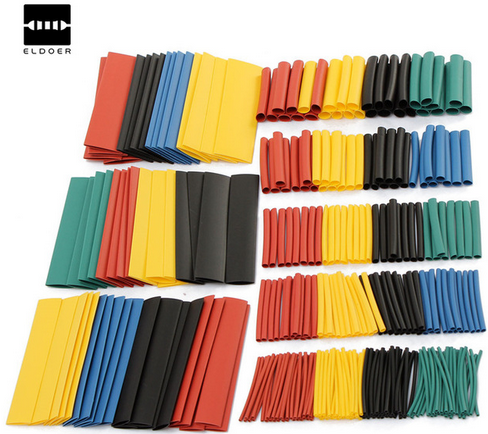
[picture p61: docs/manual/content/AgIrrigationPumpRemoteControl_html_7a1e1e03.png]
 (1) LM2596 Power Supply Output 1.5V-35V DIY Part Modules AliExpress.com (https://www.aliexpress.com/item/New-Arrival-5Pcs-DC-DC-Buck-Converter-Step-Down-Module-LM2596-Power-Supply-Output-1-5V/32809701021.html) ( $3.27/ 5PCS ) |  (2) #8-32 x 1/2” Machine Screws (5) #2 1/4” Screws BoltDepot.com (https://www.boltdepot.com/Sheet_metal_screws_Phillips_pan_head_Stainless_steel_18-8_2.aspx) (#2x1/4” $0.05/ea) BoltDepot.com (https://www.boltdepot.com/Machine_screws_Phillips_pan_head_Zinc_plated_steel_8-32.aspx) (#8-32x1/2” $0.05/ea) ( Total: $0.35 ) |  ( ~10 ) Heat-Shrinking Tubes AliExpress.com (https://www.aliexpress.com/item/328Pcs-8-Sizes-Multi-Color-Polyolefin-2-1-Halogen-Free-Heat-Shrink-Tubing-Tube-Assortment-Sleeving/32673557063.html) ( $3.12 / 328pcs )

#### C.RF Electronics ( $91.32 )

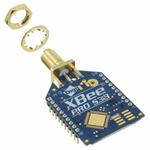
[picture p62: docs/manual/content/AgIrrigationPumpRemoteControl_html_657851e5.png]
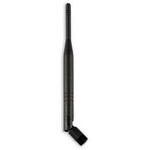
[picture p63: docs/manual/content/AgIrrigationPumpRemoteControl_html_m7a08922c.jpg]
 (2) Xbee-Pro 900Hp S3B Digimesh, 900Mhz, 250Mw, Rpsma Connector, 200Kbps https://www.arrow.com/en/products/xbp9b-dmst-002/digi-international ( $39.00/EA ) (1) for each HandRemote and (1) for each PumpController |  (2) Antenna Helical 3dB Gain 900MHz https://www.arrow.com/en/products/w1063/pulse-electronics-corporation ( $6.66/ea ) (1) for each HandRemote and (1) for each PumpController

#### D.Wire & Connectors ( $30.72 )

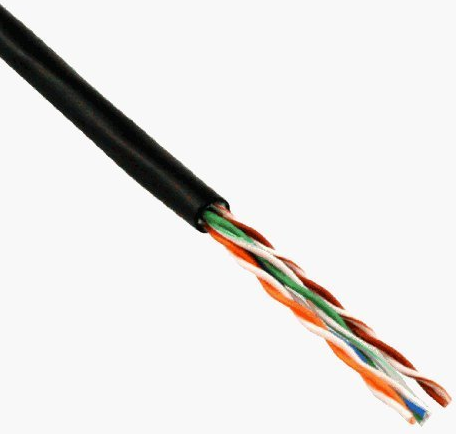
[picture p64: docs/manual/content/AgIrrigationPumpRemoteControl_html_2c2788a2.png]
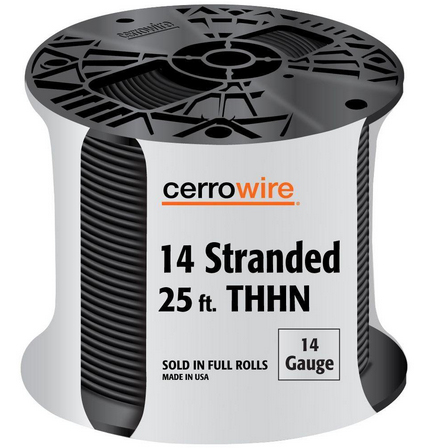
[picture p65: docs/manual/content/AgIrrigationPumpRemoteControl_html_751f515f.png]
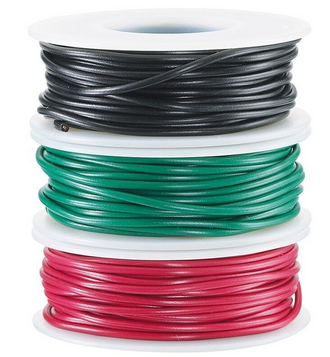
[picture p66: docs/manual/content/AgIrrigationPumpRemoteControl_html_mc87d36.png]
 (~10-feet) 24-AWG Data Cable Outdoor direct burial wire Suggest Cat5e Amazon.com (https://www.amazon.com/CERTICABLE-RJ11-RJ11-CAT-5E-OUTDOOR-TELEPHONE/dp/B00FOUQ4YM/ref=pd_day0_147_3) ( $11.50 / 50ft ) Enough to connect all accessory/power devices to the Pump-Controller |  ( 25-feet) 600V 14AWG THHN or MTW Black or Red wire (~ 1-foot ) 22AWG Solid Core wire HomeDepot.com (http://www.homedepot.com/p/Cerrowire-25-ft-14-Gauge-Single-Conductor-Black-Stranded-THHN-Wire-112-3401A/202564770)( $6.47 / 25ft ) Enough to connect RHINO P.S., SSR and Exit Panel Plug |  ( ~ 1-foot ) UL 22AWG Solid Core Hookup Wire RadioShack.com (https://www.radioshack.com/products/ul-hookup-wire-22awg-1#) ( $6.99 / 90-feet )
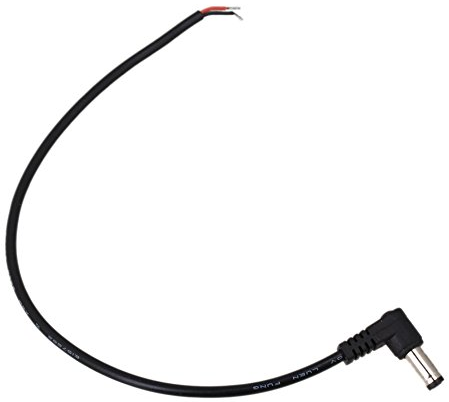
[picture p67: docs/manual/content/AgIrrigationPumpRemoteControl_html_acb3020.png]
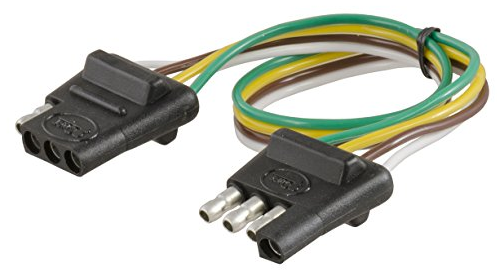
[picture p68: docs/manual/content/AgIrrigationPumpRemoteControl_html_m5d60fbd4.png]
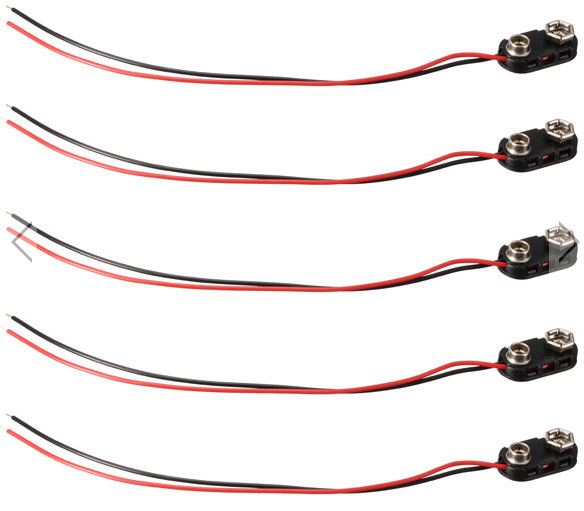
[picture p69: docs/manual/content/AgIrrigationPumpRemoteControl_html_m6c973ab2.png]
 (1) Right-Angle 5.5x2.1mm Power Plug for Arduino Power Aliexpress.com (https://www.aliexpress.com/item/2piece-22AWG-DC-tip-plug-power-connector-Single-cable-5-5-2-5mm-male-angle-L/32756147098.html) ( $1.76 / 2pcs ) Amazon.com (https://www.amazon.com/gp/product/B0111M6PIQ/) ( $4.51 / 10pcs ) |  (1) 4-Way Trailer Lights Connector Amazon.com (https://www.amazon.com/gp/product/B001EOYJEE/ref=oh_aui_detailpage_o00_s00) ( $2.32 / ea ) |  5Pcs 150mm PP3 9V Battery Clip BangGood.com (https://www.banggood.com/5Pcs-150mm-Black-PP3-9V-Battery-Clip-Snap-On-Connector-Lead-Cable-p-949544.html) ( $1.68 / 5pcs )

#### E.Tools Required ( $NA )

- 3D-Printer ( may be optional if other casing solutions are available )
- Soldering Iron and Resin Core Solder
- Needle Nose Pliers, Wire Strippers and Cutters
- Small Phillips and Flat Head Screw Drivers
- 24VDC Desktop Power Supply
- Installation also requires other tools ( not listed here )
  - see #2.INSTALLATION INSTRUCTIONS|outline

## 4.2Hand-Remote ( $69.58 )

The HandRemote is the portable remote control device used to control and monitor irrigation pumps remotely.

The following Supplies are needed to build a Hand-Remote

Total Price ( Per Hand-Remote ) = $69.58

(1) Xbee-900Hp S3B RF Module = $39.00
(1) 1” Black 22-Gauge Solid Core Hookup wire = $ 6.99
(1) 1” Red 22-Gauge Solid Core Hookup wire = Inc. Above
(1) RP-SMA High Gain Antenna = $ 6.66
(1) Arduino UNO R3 = $ 3.80
(83.8g) 3D PLA Plastic Filament ($0.03/cm3) = $ 2.82
(1) Zigbee Shield = $ 2.20
(2) Keypad / LCD Shield = $ 2.19
(2) Resistors ( 1 being 1/3 value of other ) = $ 2.28
(1) 9Vdc Battery Connector = $ 1.68
(1) On/Off Rocker Switch = $ 0.86
(1) Active Buzzer = $ 0.60
(4) #2x1/4” Screws = $ 0.30
(4) #4 x 1/4” or smaller screws = $ 0.20

The following Tools are needed to build a Hand-Remote

3D-Printer with PLA Filament
Soldering Iron & Resin Core Solder
Wire Cutters / Dikes / Strippers
Needle nose pliers

### 4.2.1Electronics Assembly

- Wiring Diagram of the HandRemote

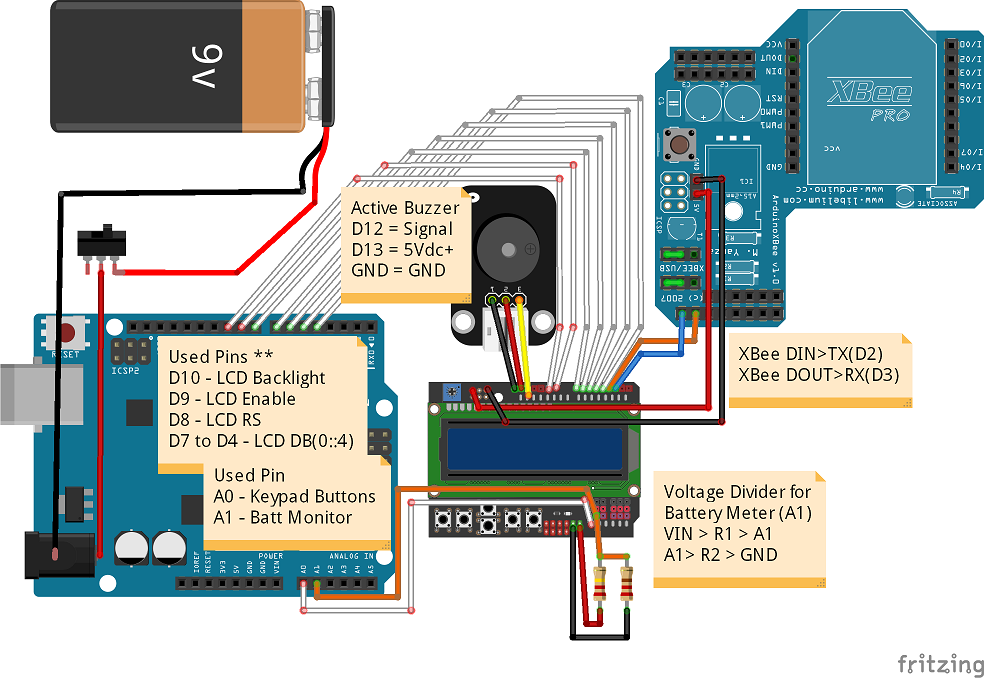
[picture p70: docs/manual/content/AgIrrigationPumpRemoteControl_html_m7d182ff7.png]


#### A.LCD Keypad Shield

1. Wire the Battery-Voltage-Divider Resistors
  a. Select (2) Resistors ( 10K-ohm up to 2M-ohm values are recommended; Arduino A1 will draw 1.6nA )
    - R1 = Larger Value Value for R1 Used = ________________
    - R2 = 1/3 the Value of R1 Value for R2 Used = ________________
  b. Solder the Resistors on the top side of the LCD Keypad Shield
    - R1 = VIN → A1
    - R2 = A1 → GND ( GND is at the Solder hole just left of VIN )
  c. Snip off the excess back-side leads

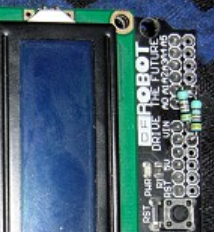
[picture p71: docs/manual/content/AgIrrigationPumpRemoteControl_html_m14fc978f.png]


The two resistors setup a voltage divider from the 9Vdc battery (which we will attach to VIN). Analog inputs on the Arduino should never exceed 5Vdc. The voltage divider will split the battery voltage to 1/3 its actual voltage. This will allow the hand-remote to monitor the battery level. The larger the resistor values the less drain on the battery; but too-large a value resistors may affect accuracy.

2. Remove the ICSP header pins on the LCD Keypad Shield
  a. Using Needle Nose pliers clamp onto an ICSP header pin on the front side of the Zigbee Shield
  b. Using Soldering Iron – Heat the solder side of the pin and pull the pin from the board
  c. Repeat steps for all remaining ICSP pins

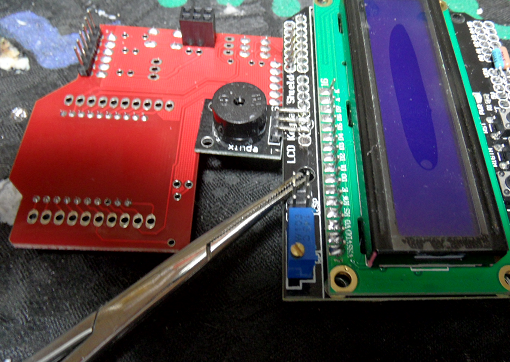
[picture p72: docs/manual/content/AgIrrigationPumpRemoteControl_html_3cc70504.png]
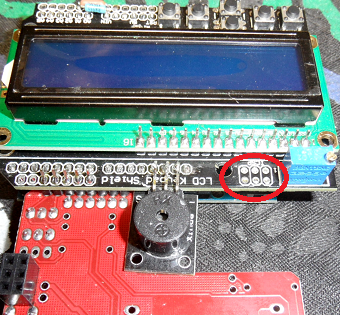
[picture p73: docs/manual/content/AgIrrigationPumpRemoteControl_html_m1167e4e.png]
 

3. Plug the LCD Keypad Shield onto the Arduino UNO

#### B.Zigbee/Xbee Shield

1. Remove Header Pins D7, D6, and D5 from the Zigbee Shield
  a. Using Needle Nose pliers clamp onto Pin D7 ( shown in picture on D7 ) of the back of the Zigbee Shield
  b. Using Soldering Iron – Heat the top of the pins solder pad and pull the pin from the board
  c. Repeat steps two more times for D6 and D5 ( moving left as D7, D6, D5 )

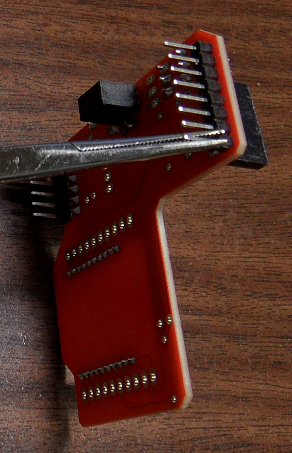
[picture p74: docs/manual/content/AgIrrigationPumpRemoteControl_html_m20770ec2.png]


2. Solder Zigbee Shield to the LCD Keypad ( Flipped upside down & with Arduino UNO attached to the LCD Keypad Shield )
  a. Insert Zigbee Shield pins D0 → D4 ( Remaining pins ) into LCD Keypad Solder Pin-holes D2→D6
    - Shifted towards center leaving 2-Pin-holes on the LCD Keypad open; as shown
  b. Position the Zigbee Shield flat with LCD Shield and Up against the LCD Shield – Requires bending the header pins a little
  c. Solder the Zigbee Shield pins to the LCD Keypad Shield

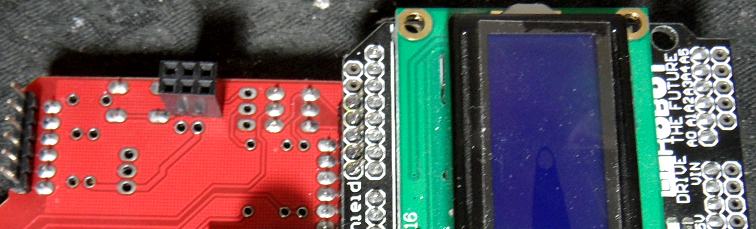
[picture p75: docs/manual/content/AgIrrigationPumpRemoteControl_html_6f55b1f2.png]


3. Wire Power to the Zigbee Shield
  a. Flip over the assembly so the LCD Keypad Shield is backside and the Zigbee Shield is front side
  b. Using two 22-Gauge Solid Core wire ( Black & Red ) Connect the LCD Keypad Shields ICSP pin header power pads to the Zigbee Shield
    - Red wire = LCD-ICSP 5V+ pin ( closest to the Top; closest to the Blue Pot ) → Zigbee Shield ( 5V ) solder pad labeled as 5V
    - Black wire = LCD-ICSP GND pin ( closest to the Top; farthest from the Blue Pot ) → Zigbee Shield ( GND ) solder pad labeled as GND
    - Note: Be sure to solder these wire into the back-side of the LCD ( as shown ) else the wires will block the rocker switch

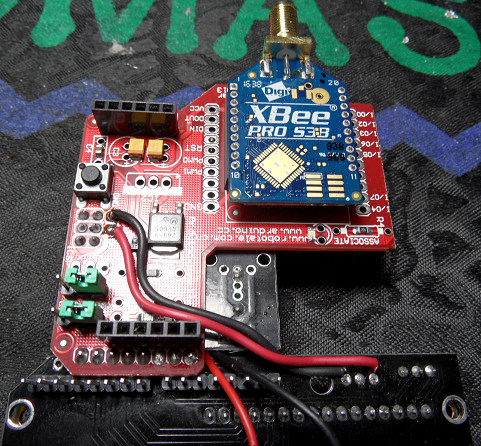
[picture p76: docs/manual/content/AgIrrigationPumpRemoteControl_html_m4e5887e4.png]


  c. The green jumpers on the Zigbee Shield should be in the USB position ( usually factory installed there ) the picture shows these in the wrong place.
- Further Reading for the Curious
  - https://www.arduino.cc/en/Main/ArduinoXbeeShield
  - https://www.arduino.cc/en/Guide/ArduinoXbeeShield

#### C.Active Buzzer

1. Solder Active Buzzer to LCD Keypad Shield
  a. Place active buzzer on edges of the Zigbee Shield as shown
  b. Solder the active buzzer pins ( S, +, - ) to the pins as shown
  c. The LCD Keypad pins ( D12, D13, and GND ) are determined according to the markings on the connected Arduino UNO.
    - 'S' pin → D12
    - '+' pin → D13
    - '-' pin → GND

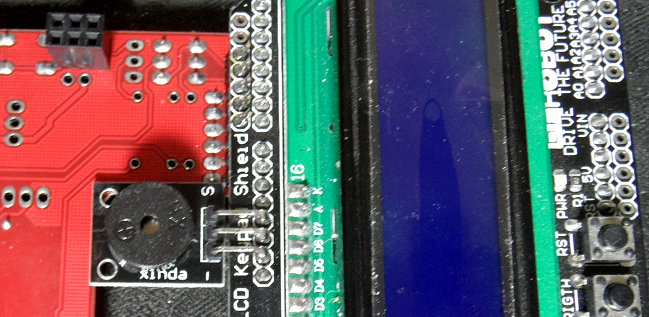
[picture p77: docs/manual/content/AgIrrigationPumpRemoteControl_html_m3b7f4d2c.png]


2. Test the Assembly
  a. Plug the Xbee Module into the Zigbee Shield
  b. Plug in the USB cord to the Arduino UNO and verify
    - The LCD screen lights
    - The LED on the Zigbee Shield next to the word “ASSOCIATE” is blinking
  c. Upload the Test.ino Firmware
    - Check that the buzzer sounds after upload ( a key-press will silence the buzzer )
    - Check that the LCD Keys work by scrolling the menu
    - Check the “Battery” meter – It should not read either 0 or 1023

### 4.2.2Hardware Assembly

#### A.3D-Prints ( $2.82 )

- Print the Following Models on a 3D-Printer
  - Files Located at https://github.com/tgit23/AgIrrigationRemoteControl/tree/master/HandRemote/3D-Prints-STL
  - Total Filament = 94-grams @ $0.03/gram ~ $2.82

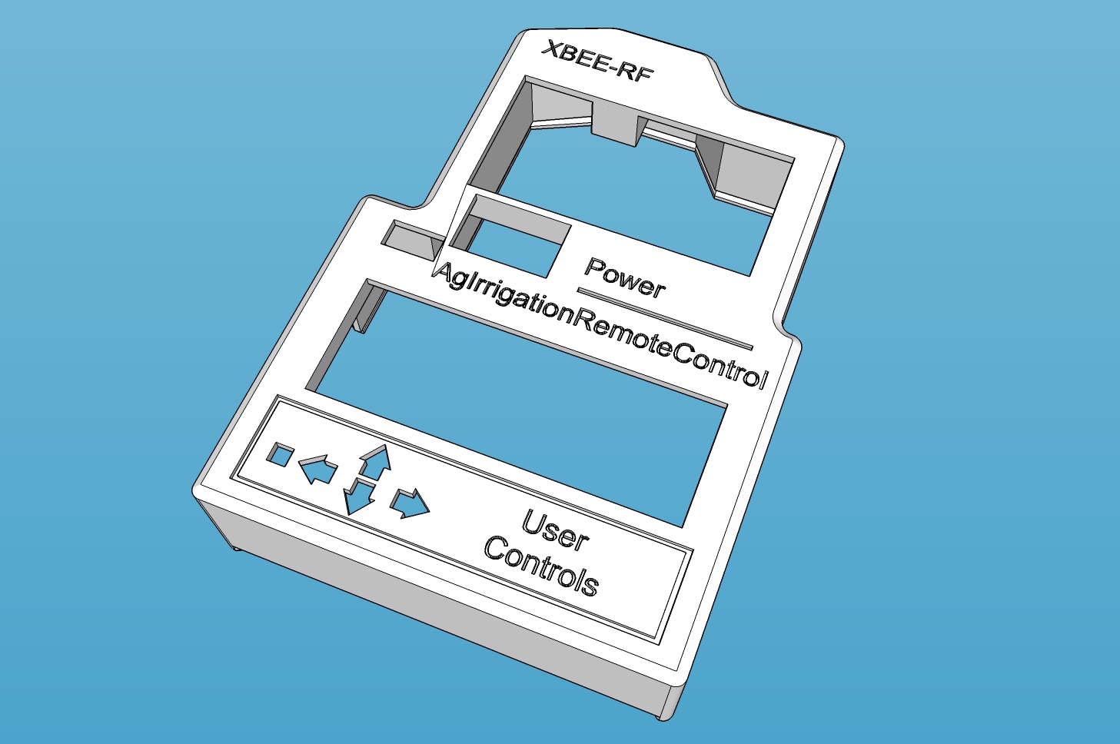
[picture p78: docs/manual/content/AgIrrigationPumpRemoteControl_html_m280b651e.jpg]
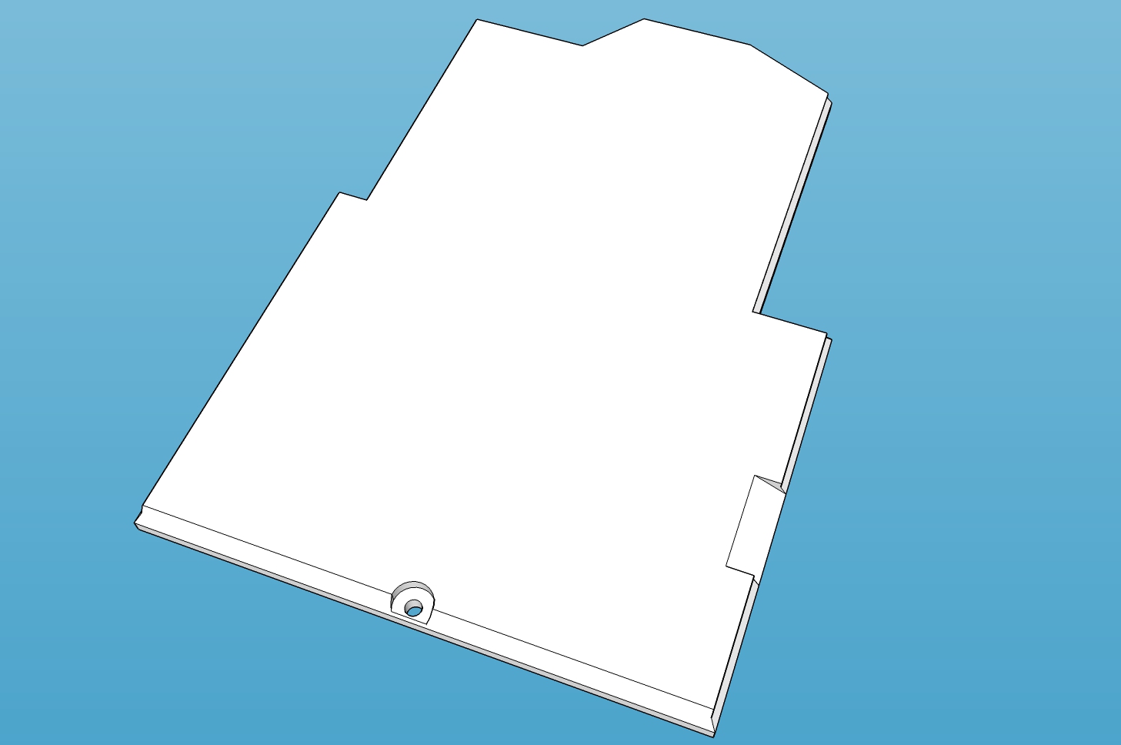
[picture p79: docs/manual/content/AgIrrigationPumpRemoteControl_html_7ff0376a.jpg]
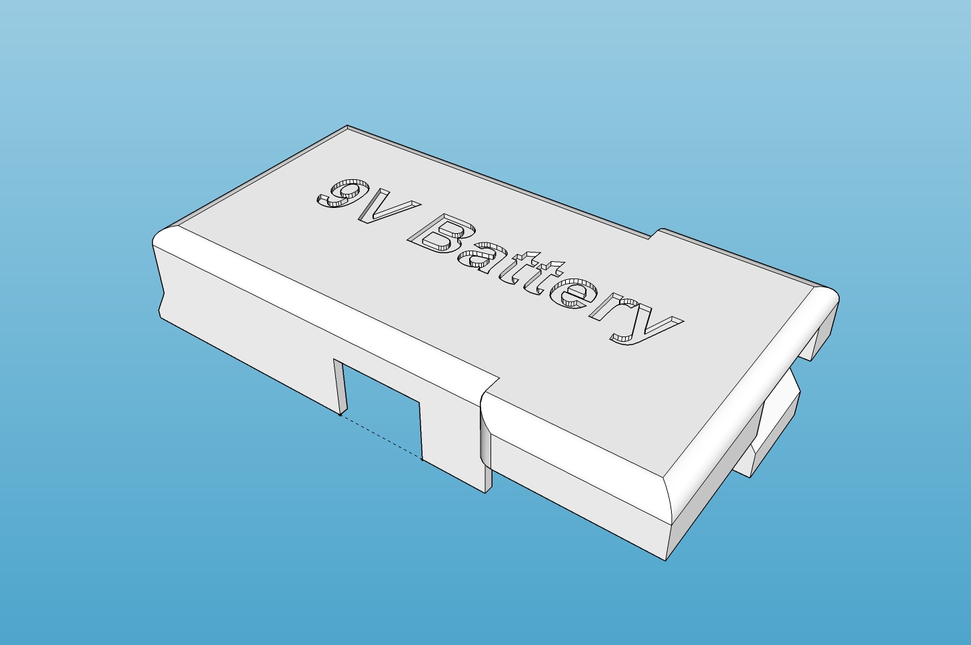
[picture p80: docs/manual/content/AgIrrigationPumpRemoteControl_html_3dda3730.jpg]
 HandRemote-Case.stl ( 62g ⁾ |  HandRemote-BackCover.stl ( 23g ⁾ |  HandRemote-BatteryCover.stl ( 4g ⁾
 HandRemote-BatteryInsulatorPlate.stl ( 2g ⁾ |  HandRemote-SideCover.stl ( 2.5g ⁾ |  HandRemote-Buttons.stl ( 1g ⁾

#### B.Install Electronics

1. Insert the Power ON/OFF Rocker Switch into the front of the case



2. Place the buttons in their proper place inside the case; using masking tape on the front-side to hold the buttons in their place

 

3. Install the LCD, Buzzer, Zigbee Electronics Assembly into the Case ( Arduino UNO Removed )
  a. Insert (4) 10mm or shorter screws – adjust tightness making sure the buttons still click ( too tight will pinch buttons down permanently )



4. Plug the Arduino UNO back onto the LCD Keypad Shield
5. Attach the Antenna to the Xbee RPSMA Connector

#### C.Wire in Battery Power

1. Install Plugs
  a. Insert the HandRemote-BatteryInsulatorPlate.stl 3D-Print inside the battery hole
  b. Route the 9Vdc Battery Power Plug from the front, around Zigbee shield, to the back



2. Wire in the Switch and Power to the Arduino UNO
  a. Solder the Black wire to the closest to UNO power-jack backside pin ( as pictured )
  b. Leaving an inch-or-so slack on the 9VDC plug; measure and cut the Red wire on the closest rocker-switch connector
  c. Strip the end and solder the wire to the rocker switch connector
  d. Strip the end of the cut left-over red wire and solder it into the “other” connector on the rocker-switch
  e. Solder the other end of the cut left-over red wire wire to the farther to UNO power-jack backside pin ( as pictured )



3. Check for Power
  a. Plug in a 9V-Battery into the 9V plug
  b. Flip the rocker-switch to power-on ( marked with a “-” ) and verify that the LCD display lights
4. Attach Covers to Case
  a. Insert the HandRemote-BatteryCover.stl 3D-Print into the cases battery-hole and snap down
  b. Slide the HandRemote-BackCover.stl 3D-Print in from the bottom then insert a screw in the bottom-center
  c. Slide the HandRemote-SideCover.stl 3D-Print in the USB side until it snaps into place

## 4.3Pump-Controller ( $82.05 )

The Pump-Controller is the irrigation pumps control device mounted next to the pumps electrical panel.

The following Supplies are needed to build a Pump-Controller

Total Price ( Per Pump-Controller ) = $82.05

(1) Xbee 900Hp Pro S3B RF Module = $39.00
(1) RP-SMA High Gain Antenna = $ 6.66
(1) Arduino UNO R3 w/Male Headers = $ 3.80
(1) LM2596 - 24Vdc to 9Vdc Step-Down Buck Converter = $ 3.27
(1) Zigbee Shield = $ 2.20

(10') Outdoor Burial data cable = $11.50
(95.2g) 3D PLA Plastic Filament ($0.03/cm3) = $ 3.87
(~12) Heat Shrinking tubes = $ 3.12
(1) 4-Way Trailer Lights Plug = $ 2.32
(1) Right-Angle 9VDC Power Plug = $ 1.76
(1) #2x1/4” Screw = $ 0.05

(1) 50x70cm Perfboard = $ 1.56

(9) Screw Terminal Blocks = $ 2.15
(2) 2-PIN or 4-PIN Female DuPont Pin Headers = $ 0.79
(2) 3-PIN or 4-PIN Female DuPont Pin Headers = Inc. Above
(2) 6-PIN Male DuPont Headers ( Included with Arduino Uno )
(1) 2-PIN Male DuPont Header ( Included with Arduino Uno )
(18”) 22 Gauge Solid Core Hook-up wire ( listed with Hand-Remote )

The following Tools are needed to build a Pump-Controller

3D-Printer with PLA Filament
24Vdc Desktop Power Supply
Soldering Iron & Solder
Wire Cutters / Dikes / Strippers
Small flat screw driver

### 4.3.1Electronics Assembly

- Wiring Diagram of the Pump Controller - ( Screw Terminal Perfboard → Zigbee Shield → Arduino UNO )



#### A.3D-Prints ( $0.20 )

- Print the Following Model on a 3D-Printer
  - File Located at https://github.com/tgit23/AgIrrigationRemoteControl/tree/master/PumpController/3D-Prints-STL
  - Total Filament = 6.3 cm3 @ $0.03/cm3 ~ $0.20



PumpController-PerfboardCover.stl ( 6.3 cm³ ⁾

#### B.Perfboard Assembly

1. Prepare Female DuPont Headers
  a. If using a 4-PIN instead of 2-PIN Female DuPont Connector; Remove the outer pins on one 4-PIN female header ( POWER )
  b. Using a 4-PIN Female DuPont Header; Remove every other pin -OR- Using a 3-PIN Female DuPont Header; Remove center pint ( RX/TX )



2. Install Headers
  a. Remove the (2) Green Jumpers on the Zigbee Shield
  b. Plug the Zigbee Shield onto the Arduino UNO
  c. Plug a 6-PIN Male Header into the Analog Header of the Zigbee Shield ( A5 → A0 )
  d. Plug a 6-PIN Male Header into the Digital Header of the Zigbee Shield ( D2 → D7 )
  e. Insert the POWER female header from step #1.a into the Zigbee Shield holes labeled 5V & GND ( next to the reset button )
    - Plug a 2-PIN Male Header into the top of the POWER female header
  f. Insert the RX/TX female header from step #1.b ACROSS the two center male headers (XBEE/USB) pins of the Zigbee Shield



3. Solder the header pins to a 5cmx7cm 2.54mm pitch Perfboard
  a. Align and place the Perfboard onto the header pins so that the Perfboard edges match the Arduino Uno edges
  b. Solder the header pins to the Perfboard



4. Solder the Zigbee female POWER header pins
  a. Unplug the Arduino UNO from the Zigbee Shield leaving the Perfboard attached
  b. Solder the female POWER header pins to the holes of the Zigbee shield



5. Add wires to the header pins
  a. Cut (10) wires approximately 1” long and strip one end.
  b. Cut (2) wires approximately 3” long and strip one end.
  c. Gather (2) Pulled male pin headers ( from ICSP Hand-Remote ) or two more 1” wires



  d. Attach (2) Pin Headers or Small wires from the Top-side of the Perfboard across RX/TX female pin headers and solder to D2, D3 Digital pins
  e. Unplug the Perfboard from the Zigbee Shield
  f. Insert (6) 1” wires from the Zigbee-side of the Perfboard into the holes just below the analog male pin headers, bend and solder
  g. Insert (4) 1” wires from the Zigbee-side of the Perfboard into the 4-right (D4-D7) holes just above the digital male pin headers, bend and solder
  h. Insert (2) 3” wires from the Zigbee-side of the Perfboard into the right of the POWER male pin headers ( Center-2 ), bend and solder
6. Install the Screw Terminals
  a. Place the HandRemote-PerfboardCover.stl 3D-Print on the top of the Perfboard
  b. Insert (3) 2x Screw Terminals sliding the blocks together at their edges
  c. Insert (2) 2x Screw Terminals along the Digital section with the same method above
  d. Insert (2) 2x Screw Terminals along the 5VDC section ( same as above )
  e. Insert (2) 2x Screw Terminals along the GND section ( same as above )

Note: If drilling out the holes is required; drill from the soldering side as to not dismount the solder-to pads



7. Solder the Screw Terminals to their corresponding header wires
  a. Turn the Perfboard over holding the screw terminals into place
  b. Sold each screw terminal pin to the Perfboard
  c. Pull the Insulation off the wires, bend them flat with the Perfboard and solder them to their corresponding pin ( See picture or Wiring Diagram )



### 4.3.2Hardware Assembly

#### A.3D-Prints ( $3.87 )

- Print the Following Models on a 3D-Printer
  - Files Located at https://github.com/tgit23/AgIrrigationRemoteControl/tree/master/PumpController/3D-Prints-STL
  - Total Filament = 129-grams @ $0.03/gram ~ $3.87

 PumpController-Case.stl ( 98g ⁾ |  PumpController-Cover.stl ( 25g ⁾ |  PumpController-AntennaCover.stl ( 1g ⁾
 PumpController-XbeeInsulatorPlate.stl ( 1g ) |  PumpController-CableClampCover.stl ( 3g ) |  PumpController-CableClampCover-2HoleInsert.stl ( 1g ⁾

#### B.Install Electronics

1. Install UNO and Zigbee into the Case
  a. Remove the Screw Terminal Perfboard if attached and connect the Arduino UNO & Zigbee Shield
  b. Insert the Uno/Zigbee assembly into the case letting the USB and power Jack sit on each side of the case stub.



2. Install the XBEE module
  a. First slide the XBEE RPSMA Connector into the case slot
  b. Then lift the XBEE module into to place and plug it into the Zigbee Shields Xbee plug-in



3. Install the Xbee Antenna Cover
  a. Slide the AntennaCover.stl 3D-Print onto the RPSMA connector from the outside of the case



  b. Attach the washer and nut and tighten



#### C.Install Cable

1. Wire the LM2596-DC-Converter Module to one end of the cable
  a. Cut a 10' length of Outdoor data cable with 3 or more leads
  b. Strip off the outer insulation of one end
  c. Cut a 10' length of Outdoor data cable
  d. Strip off the outer insulation of one end approximately 4” back
  e. Strip off the ends of the Orange and Brown twisted pairs just enough to fit in the LM2596 solder holes
    - Solder the Orange twisted pair to the LM2596 Module pad labeled IN+
    - Solder the Brown twisted pair to the LM2596 Module pad labeled IN-
2. Wire the Right-Angle 5.5x2.1mm DC Power Plug to the LM2596-DC-Converter Module
  a. Cut the Right-Angle DC Power plug cords length to approximately 3”
  b. Strip off the outer insulation approximately 1” back
  c. Strip off the ends of the Red and Black wire just enough to fit in the LM2596 solder holes
    - Solder the Red Wire to the LM2596 Module pad labeled OUT+
    - Solder the Black Wire to the LM2596 Module pad labeled OUT-



3. Adjust the LM2596 Module to produce 9Vdc from 24Vdc
  a. Clip on a 24Vdc+ desktop power supply to IN+ and IN-
  b. Attach a Voltmeter to OUT+ and OUT-
  c. Adjust the Blue Pot till the measured voltage is 9Vdc on OUT+ and OUT-
4. Attach the Male end of the 4-way Trailer Lights Connector to the other end of the cable ( Female end used in #4.4.1.2.Pump-Panel Exit Cable|outline )
  a. Cut the male end of the 4-way connector wires leaving about 1” of Wire from the plug
  b. Strip all the wires back about 1/4”
  c. Slide on heat shrinking tube for each wire and the bundle of wires
  d. Solder the following Cable pairs to the connector
    - Blue twisted pair to the White connector wire
    - Brown twisted pair to the Brown connector wire
    - Orange twisted pair to the Yellow connector wire
    - Green twisted pair to the Green connector wire



5. Install the Cable into the Pump-Controller Box
  a. Insert the cable into the CableClampCover.stl 3D-Print and insert it with the LM2596 Module into the Case as shown
  b. Insert the CableClampCover-2HoleInsert.stl into the open holes of the CableClampCover.stl
  c. Plug the Power Plug plug into the Arduino UNO
  d. Slide the CableClampCover.stl into the slot provided by the case as shown



6. Attach Perfboard and Wire to Cable
  a. Place the XbeeInsulatorPlate.stl 3D-Print over the Xbee Module ( Protects it from shorting against the Perfboard )
  b. Carefully plug the Perfboard back onto the Zigbee Shield
  c. Strip the ends of the BLUE/GREEN twisted pairs of the Cable and connect them to the Screw Terminals
    - BLUE twisted pair to D7
    - GREEN twisted pair to D6



## 4.4Installation-Kit ( $98.07 )

The Installation-Kit is the items that will be used to control the irrigation pump inside the pumps electrical panel.

The following Supplies are needed for an Installation-Kit Total Price ( Per Installation-Kit ) = $98.07 (1) RHINO 480V 3-Phase to 24VDC Power Supply = $59.00 (1) 600VAC Solid State Relay N.O. Random = $24.50 (25-feet) 600V Wire 14AWG THHN or MTW wire = $ 6.47 (6”) DIN Rail ( Sold in 1-Meter / (3) ) = $ 8.00 (2) #8-32 x 1/2” Machine Screws = $ 0.10 (1) Wood screw (1) 4-Way Trailer Lights Connector ( listed with Pump-Controller ) (~4) Heat Shrinking Tubes ( listed with Pump-Controller ) | The following Tools are needed to create an Installation-Kit Soldering Iron & Resin Core Solder Wire Cutters / Dikes / Strippers

#### A.DIN Rail & Components

1. Prepare Din Rail
  a. Cut a section of DIN Rail 6” long
  b. Attach the Power Supply Unit
  c. Attach the Solid State Relay (SSR)
2. Add Hook-Up Wires to the Solid State Relay (SSR)
  a. Run a 600VAC 14-Gauge BROWN wire from 24VDC(-) on top of the Power Supply to A1 of the Solid State Relay
  b. Attach a 4-foot long stretch of 600VAC 14-Gauge RED wire from SSR (15); Installs later to the AUTO selector switch
  c. Attach a 4-foot long stretch of 600VAC 14-Gauge RED wire from SSR (16); Installs later to the Contactor Activation Coil

#### B.Pump-Panel Exit Cable

1. Create the Pump-Panel Exit Cable that will exit the Pumps Electrical Panel and plug into the Pump-Controllers cable.
  a. With the Female end of the 4-way Trailer Lights Connector ( Male side used in #4.3.2.3.Install Cable|outline )
    - Cut the wires approximately 1” from the plug
    - Install Heat Shrinking tube to the wires
    - Strip and Solder the plug wires
      - White plug wire to 4-feet of Blue 600V 14AWG wire
      - Brown plug wire to 4-feet of Brown 600V 14AWG wire
      - Yellow plug wire to 4-feet of Orange 600V 14AWG wire
      - Leave the Green wire snipped at the end ( It is not used but may connect to an auxiliary contactor later )



#### C.Miscellaneous Items

- Include the following items with the Installation-Kit
  - This document printed on paper
  - Automatic Center Punch
  - #8-32 Tap and #29 Drill Bit
  - (2) #8-32 x 1/2” Machine Screws
  - (1) Wood Screw for mounting the Pump-Controller

# 5.SYSTEM SETUP

- This section is a guide for
  - Configuring the Xbee RF Module
  - Uploading Firmware onto the Hand-Remote and Pump-Controller's micro-controller ( i.e. Arduino UNO )
  - Details about customizing the firmware to match a users needs ( Such as adding a pressure meter or water-level meter )
- This section only needs to be read if:
  - The project is built from scratch - In which case the firmware must be uploaded to both the Hand-Remote and Pump-Controller
  - The current setup has changed - If a digital pressure meter or ultrasonic meter ( water-level ) is added; firmware must represent those additions
  - Special operations are required - Experienced programmers can program the units to operate however they wish

## 5.1Adding Expansions

1. Follow the steps in #5.2.Uploading Firmware|outline to Step #4 for the Hand-Remote firmware; Hold off on Step #5; “Compile & Upload”
2. Once the file is open in Arduino Sketch IDE; locate the following code-block which should be right at the top

//=====================================================================================================================

//------------------------------ SIMPLE USER CONFIGURATION SETTINGS ---------------------------------------------------

//=====================================================================================================================

#define BUILD_VERSION 20170622 // Release Version used to Build the Unit ( without the dots )

#define TRANSCEIVER_ID 1 // Unique numeric (ID)entity for this Unit(1-15)

#define XBEECONFIG 0 // Configure the XBEE using XCTU Digi Software by setting this to 1

#define ULTRASONIC_WATER_LEVEL_INSTALLED 0 // 0 = NO, 1 = YES ( Wire TRIG -> D4, ECHO -> D5 )

#define WATER_PRESSURE_INSTALLED 0 // 0 = NO, 1 = YES ( Wire SENSE -> A3 )

//^^^[ END - SIMPLE USER CONFIGURATION SETTINGS ]^^^^^^^^^^^^^^^^^^^^^^^^^^^^^^^^^^^^^^^^^^^^^^^^^^^^^^^^^^^^^^^^^^^^^^

3. As described within the comments ( text following '//' )
  a. Change ULTRASONIC_WATER_LEVEL_INSTALLED to a '1' if a water-level sensor has been attached to the Pump-Controller.
  b. Change WATER_PRESSURE_INSTALLED to '1' if a digital pressure sensor has been attached to the Pump-Controller.
4. Now proceed to Step #5 in #5.2.Uploading Firmware|outline and Compile & Upload the changes just made

## 5.2Uploading Firmware

1. Install Arduino Sketch IDE ( If NOT installed already ) https://www.arduino.cc/en/Main/Software
2. Install the PeerIOSerialControl Library ( If NOT installed already )
  a. In a web-browser; go to https://github.com/tgit23/PeerIOSerialControl
  b. On Green Clone or download Choose Download Zip
  c. Save to a place you'll remember – like Documents or Desktop
  d. Run the Arduino Sketch IDE
  e. Choose Menu Item Sketch → Include Library → Add .zip Library
  f. Select the PeerIOSerialControl Library file saved in step 'c' above
3. Install the SSoftwareSerial Library - Required by the Hand-Remote Firmware ( If NOT installed already )
  a. In a web-browser; go to https://github.com/tgit23/SSoftwareSerial
  b. Click on file SSoftwareSerial.zip ; Then click on 'Download' above 'View Raw'
  c. Save to a place you'll remember – like Documents or Desktop
  d. Run the Arduino Sketch IDE if not already open from step #1
  e. Choose Menu Item Sketch → Include Library → Add .zip Library
  f. Select the SSoftwareSerial.zip Library file saved in step 'c' above
4. Download the Firmware
  a. In a web-browser; go to https://github.com/tgit23/AgIrrigationRemoteControl
  b. On Green Clone or download Choose Download Zip
  c. Save to a place you'll remember – like Documents or Desktop
  d. Unzip the Folder
  e. In Arduino Sketch IDE choose File → Open and Select
    - File HandRemote.ino for the HandRemote Firmware
      - Location Example: \Downloads\AgIrrigationRemoteControl-master\AgIrrigationRemoteControl-master\HandRemote
    - File PumpController.ino for the PumpController Firmware
      - Location Example: \Downloads\AgIrrigationRemoteControl-master\AgIrrigationRemoteControl-master\PumpController\PumpRemote
5. Compile and Upload the Firmware
  a. Plug in a USB cable from the Computer to the unit
  b. Select the Port the units USB is connected to; in Sketch menu Tools → Port
    - To determine Port; Open Windows Device Manager → Ports ( COM & LPT ) a new COM?? port appears right after plugging in the cable
  c. Select the Board; Sketch menu Tools → Board → Arduino/Genuino UNO
  d. In Arduino Sketch IDE; Press the Right-Arrow next to the Check mark in the Top-Left Corner to upload the firmware onto the unit

## 5.3Xbee RF Configuration

The XBEE RF Module is setup from the factory to work without any additional changes. However, often it is very wise to assign non-factory setting in order to keep your RF communications from being interfered with by other XBEE devices in the neighborhood. Changes to the ID Network ID ( described below ) will need to be preformed on all Hand-Remotes and all Pump-Controllers

1. Upload Firmware with XBEE Configuration Set
  a. To change the XBEE settings – Follow Steps #1 to #3 in #4.2.A SYSTEM OPERATIONS|Firmware|Uploading

With the Firmware file open find the following line of code; which should be very close to the top

#define XBEECONFIG 0 // Configure the XBEE using XCTU Digi Software by setting this to 1

Change it to

#define XBEECONFIG 1 // Configure the XBEE using XCTU Digi Software by setting this to 1

  b. Then proceed to upload the firmware to the Unit as outline in Step #4 in #4.2.A SYSTEM OPERATIONS|Firmware|Uploading
2. Install Digi-XCTU
  a. The Digi XCTU software can be gotten from https://www.digi.com/products/xbee-rf-solutions/xctu-software/xctu
3. Run Digi-XCTU



  a. Using the + ( Add Radio Modules ) mark in the top left corner enter the unit's COM port ( The Arduino COM Port )
  b. The main values that may be of interest are:
    - ID Network ID - This sets a Unique “Channel” to keep your units communications separate from any others out there (Must be same on all units)
    - PL TX Power Level - If devices are close; a lower power setting can preserve battery life
4. Save Settings to the Xbee and Reload Firmware
  a. Be sure to click the “Write” button in XCTU to save any settings that were made
  b. Close XCTU
  c. In Arduino Sketch IDE restore the following line to its original

#define XBEECONFIG 0 // Configure the XBEE using XCTU Digi Software by setting this to 1

  d. Upload the Firmware to the Unit again as outline in Step #4 in #4.2.A SYSTEM OPERATIONS|Firmware|Uploading

## 5.4Customizing Firmware

### 5.4.1Pump-Controller

- The Pump-Controller Firmware preforms the following duties
  - Wait for Hand-Remote Requests and generate responses
  - Calculate values ( Virtual-Pin Values ) for special devices that require a process to obtain a value ( like ping/echo for Ultrasonic level measurements )
  - Retain a Power-Off status after a power failure has occurred at the pump ( Arduino is designed to keep digital pins low after a power failure )

NOTE: Wiring, Timing, and Almost all system functions are implemented on the Hand-Remote Firmware

#### A.Virtual Pins

Virtual pins are non-hardware related value identifiers that are created and assigned by the Pump-Controller firmware and then accessed by the Hand-Remote as a “Pin” value. An example case is the ultrasonic water level; The pump-controller firmware pings and times an echo of the ultrasonic distance meter using its D4 ( Trigger ) and D5 ( Echo ) pins and stores the measured value on “virtual pin 64”. When the Hand-Remote queries for a value on pin-64 it actually gets the measured value which is a combination of D4 & D5 already calculated by the Pump-Controller.

- An Example of a Virtual Pin setup on the Pump-Controller firmware

void loop(){

XBee.Available();

#if US_PRESENT>0

// Read UltraSonic water level

int ulCurrentTime = millis();

if ( ulCurrentTime > ulLastPing + 1000 ) {

XBee.VirtualPin(64, sonar.ping_in() );

ulLastPing = ulCurrentTime;

}

#endif

}

### 5.4.2Hand-Remote

- The Hand-Remote Firmware preforms the following duties
  - Storing the alarm values in non-volatile memory (EEPROM) so user values and settings aren't lost every-time the power is turned off
  - Updating the current status (MAIN Values) of the Menu-Items and checking for Alarm boundaries.
  - Processes User Input
    - UP/DOWN user buttons will increments or decrements the Menu-Items
    - RIGHT/LEFT user buttons will increments or decrements the Sub-Function of each Menu-Item
    - ENTER ( square ) user button will preform a value SET; or update MAIN values when they are being displayed
  - Menu-Items are associated/connected to a Device and its Hardware Pin
    - Device - Example; The Hand-Remote running this firmware, or a Pump-Controller device controlling a pump
    - Pin - Example; 7(for D7) or A2 as identified inside the Pump-Controller Unit or by the Arduino UNO board
  - Menu-Items have Sub[?] Values, such as
    - The actual/read/MAIN value of the Menu-Items - Example; Power is currently either ON/OFF ( current status )
    - SETting a Value for the Menu-Item - Example; SET the Power to either ON/OFF
    - Setting a Too LOw ALARM Value - Example; When pressure is below 10 sound the Low Alarm
    - Setting a Too HIgh ALARM Value - Example; When pressure is above 100; sound the High Alarm
  - Menu-Items can have Option Values ( An Optional way of handling Menu-Item value assignments )
    - Options associates a common MAIN-Value to a Text identifier; for example ON/OFF.
    - A Menu-Items value must be a select-able set of Options or a Number but cannot be both.
    - The maximum number of options is limited by program line #define MAXOPTIONS 2 // Maximum number of Menu Item Options allowed
  - Menu-Item Limits
    - Program line #define MAX_MENU_ITEMS 15 // Maximum number of Menu Items allowed ( using 71% dynamic memory )
    - Determines the maximum number of menu-items that can exist; it can be increased slightly but may produce memory warnings.

#### A.Adding & Deleting Devices

- The Hand-Remote Firmware tracks ALL the associated devices it can control and monitor.
  - To add another Device to the control and monitoring system
    - Add any Unique Name to the Comma separated list of devices on the Program Line shown below
      - uDevices HandRemote, CanalPump, DitchPump; // Name and Define all controllable devices in the System
    - At the top of the SetupMenu() function; Assign the Unique Named device a .Text Identifier ( Used in the Menu )
    - At the top of the SetupMenu() function; Assign the Unique Named unit Unit's .Transceiver_ID number assigned in the units firmware
      - Example Program Line CanalPump.Text = "Canal Pump"; CanalPump.TransceiverID = 10;
  - Delete devices by removing the items in the adding devices listed above.
    - Note: If there is no conflict of Transceiver_ID's or naming there really isn't a substantial need to remove a “missing” device from the system.

#### B.Creating a Menu-Item

1. Find the SetupMenu() function in the Hand-Remote firmware file; This is where all the Menu-Items are defined
2. Indexing - Determine where in the list of Menu-Items you'd like the new item to appear
  a. All Items MUST BEGIN with line MenuItemsIdx++; except the very first item ( Usually the Hand-Remote battery status )
  b. The line above increments the Indexing ( line count ) to allow the new menu-item to exist
  c. Items that do not have [MenuItemsIdx] indexing are used in other places of the firmware and should NEVER BE CHANGED!
3. Device - Assign the device this Menu-Item is attached to
  a. This is the Device's Unique Name given in Step #A|Adding & Deleting Devices
  b. The unit is generally a named Pump-Controller device with an assigned Transceiver_ID.
4. Pin – Assign the Hardware Pin of the device that the Menu-Item will control or monitor
  a. The hardware pin is the terminal inside the controlling device box ( pump-controller ) that the control/monitor equipment is wired to
  b. NOTE: Digital Pins ( D4 → D7 ) are identified by only their number ( e.g. 4 = D4 ) whereas Analog pins require both letter and number ( e.g. A2 ).
    - Digital Example; Menu[MenuItemsIdx].Pin=7;
    - Analog Example; Menu[MenuItemsIdx].Pin=A3;
5. Text - Assign the Menu-Item a defining Text
  a. The text is what will be displayed on the Hand-Remote display
    - Example; Menu[MenuItemsIdx].Text=”Power”;
6. Options - Determine IF the Menu-Item will have textual “Options” or is just a numerical value
  a. If the Menu-Item will report numerical values such as Voltage, Water Level, Pressure etc... Skip to step #5
  b. Determine the Menu-Items Options and assign each a;
    - Text Example; Menu[MenuItemsIdx].Option[0].Text = “On”;
    - Value Example; Menu[MenuItemsIdx].Option[0].Value = HIGH;
7. Sub[SET] – Determine IF the user should be allowed to set a value on the Location ( Output Pins like turning Power ON/OFF )
  a. If the Menu-Item is for monitoring status and the user will not be setting its value (INPUT)... Skip to step #7
  b. If the Menu-Item needs to allow the user the ability to set the value ( OUTPUT )
    - Set the “State” to SETTABLE to allow the user to SET the value
    - Example; Menu[5].Sub[SET].State = SETTABLE;
8. Sub[??ALARM] – Determine if the value should be monitored with an alarm
  a. LOALARM
    - If the Menu-items value is numeric and the value should be checked for getting too small
    - OR If the Menu-item value is an “option” and the value should be checked to see if it is EQUAL
      - Assign an LOALARM identifier Example; Menu[5].Sub[LOALARM].ID = 'c';
  b. HIALARM
    - If the Menu-items value is numeric and the value should be checked for getting too large
    - OR If the Menu-Item value is an “option” and the value should be checked to see if it is NOT-EQUAL
      - Assign a HIALARM identifier Example; Menu[5].Sub[HIALARM].ID = 'C';
9. Proceed to #4.3.2.3.Updating Changes|outline

#### C.Deleting a Menu-Item

1. Find the menu item you'd like to delete by identifying it by its' Menu[MenuItemIdx].Text setting
2. Select ALL the items from MenuItemsIdx++; up to but no including the next MenuItemsIdx++;
3. Press delete

#### D.Menu-Item Setup ( Example )

The menu items are defined in the SetupMenu() Function identified by line 'void SetupMenu() {'. Each item in the Menu has a numeric index (i.e. Menu[index-#] below the constant 'MONITOR' is assigned index-0 and 'PUMPIDX' is assigned index-1).

//=====================================================================================================================

//------------------------------ MENU STRUCTURE ( ADVANCED CONFIGURATION ) --------------------------------------------

//=====================================================================================================================

/******************************************************************************************************************//**

* @brief Setup the LCD menu

* @remarks

* - Allows a single spot customization to the user interface

* - Display will show the items in the same order as they are defined here

* @code

* exmaple code

* @endcode

**********************************************************************************************************************/

uDevices HandRemote, CanalPump, DitchPump; // Name and Define all controllable devices in the System

void SetupMenu() {

HandRemote.Text = "Hand Remote"; HandRemote.TransceiverID = TRANSCEIVER_ID;

DitchPump.Text = "Ditch Pump"; DitchPump.TransceiverID = 10;

CanalPump.Text = "Canal Pump"; CanalPump.TransceiverID = 11;

//BATT (idx-0) ----------------------------

Menu[BATT].Device = HandRemote;

Menu[BATT].Pin = A1; // Battery level is gotten from the Hand-Remote pin A1

Menu[BATT].Text = "Battery(B)"; // Create a menu item for monitoring the Battery

Menu[BATT].ValueModifier = BATTVOLTS; // Modify raw value to show voltage

Menu[BATT].Sub[LOALARM].ID = 'b'; // A Low Alarm is identified by a lower-case 'b'

//-----------------------------------------

MenuItemsIdx++;

idx = MenuItemsIdx; // !!!-- Set where the Menu will start --!!!

Menu[MenuItemsIdx].Device = DitchPump;

Menu[MenuItemsIdx].Pin = 7; // Power is set/got on all Pump-Controller's on pin [D7]

Menu[MenuItemsIdx].Text = "Power(P)"; // Create a menu item for Power Control

Menu[MenuItemsIdx].Sub[SET].State = SETTABLE; // Allow this Value to be 'SET' by the user

Menu[MenuItemsIdx].Sub[LOALARM].ID = 'p'; // A Low Alarm is identified by a lower-case 'p'

Menu[MenuItemsIdx].Sub[HIALARM].ID = 'P'; // A High Alarm is identified by an upper-case 'P'

Menu[MenuItemsIdx].Option[0].Text = "Off"; // Power can be "Off" - Option #0 = Off

Menu[MenuItemsIdx].Option[0].Value = LOW; // "Off" will be the value 'LOW" - Off = LOW

Menu[MenuItemsIdx].Option[1].Text = "On"; // Power can be "On" - Option #1 = On

Menu[MenuItemsIdx].Option[1].Value = HIGH; // "On" will be the value 'HIGH' - On = HIGH

Menu[MenuItemsIdx].LastOptionIdx = 1; // Last Option Index defined - Number of Options - 1

//-----------------------------------------

#if ULTRASONIC_WATER_LEVEL_INSTALLED>0

MenuItemsIdx++;

Menu[MenuItemsIdx].Device = DitchPump;

Menu[MenuItemsIdx].Pin = 64; // Water Level is read from VIRTUAL (Pump-Controllers firmware) pin 64

Menu[MenuItemsIdx].Text = "Water (L)"; // Create a menu item for Water Level Transducer

Menu[MenuItemsIdx].Sub[LOALARM].ID = 'l'; // A Low Alarm is identified by a lower-case 'l'

Menu[MenuItemsIdx].Sub[HIALARM].ID = 'L'; // A High Alarm is identified by an upper-cse 'L'

#endif

//-----------------------------------------

#if WATER_PRESSURE_INSTALLED>0

MenuItemsIdx++;

Menu[MenuItemsIdx].Device = DitchPump;

Menu[MenuItemsIdx].Pin = A3; // The 'signal' is gotten on all Pump-Controllers on pin [A3]

Menu[MenuItemsIdx].Text = "Pressure(R)"; // Create a menu item for the Primary Pressure Transducer

Menu[MenuItemsIdx].ValueModifier = PRESSURE; // Modify value to display PSI instead of MPa

Menu[MenuItemsIdx].Sub[LOALARM].ID='r'; // A Low Pressure alarm is identified by a lower-case 'r'

Menu[MenuItemsIdx].Sub[HIALARM].ID='R'; // A High Pressure alarm is identified by an upper-case 'R'

#endif

/*// UN-COMMENT BELOW FOR A SECOND PUMP-CONTROLLER ( NAMED "Canal Pump" ) WITH TRANSCEIVER_ID = 11

//-----------------------------------------

MenuItemsIdx++;

Menu[MenuItemsIdx].Text = "Power(C)"; // Create a menu item for Power Control

Menu[MenuItemsIdx].Device = CanalPump;

Menu[MenuItemsIdx].Pin = 7; // Power is set/got on all Pump-Controller's on pin [D7]

Menu[MenuItemsIdx].Sub[SET].State = SETTABLE; // Allow this Value to be 'SET' by the user

Menu[MenuItemsIdx].Sub[LOALARM].ID = 'c'; // A Low Alarm is identified by a lower-case 'p'

Menu[MenuItemsIdx].Sub[HIALARM].ID = 'C'; // A High Alarm is identified by an upper-case 'P'

Menu[MenuItemsIdx].Option[0].Text = "Off"; // Power can be "Off" - Option #0 = Off

Menu[MenuItemsIdx].Option[0].Value = LOW; // "Off" will be the value 'LOW" - Off = LOW

Menu[MenuItemsIdx].Option[1].Text = "On"; // Power can be "On" - Option #1 = On

Menu[MenuItemsIdx].Option[1].Value = HIGH; // "On" will be the value 'HIGH' - On = HIGH

Menu[MenuItemsIdx].LastOptionIdx = 1; // Last Option Index defined - Number of Options - 1

//-----------------------------------------

MenuItemsIdx++;

Menu[MenuItemsIdx].Text = "Pressure(F)"; // Create a menu item for the Primary Pressure Transducer

Menu[MenuItemsIdx].Device = CanalPump;

Menu[MenuItemsIdx].Pin = A3; // The 'signal' is gotten on all Pump-Controllers on pin [A3]

Menu[MenuItemsIdx].ValueModifier = PRESSURE; // Modify value to display PSI instead of MPa

Menu[MenuItemsIdx].Sub[LOALARM].ID='f'; // A Low Pressure alarm is identified by a lower-case 'r'

Menu[MenuItemsIdx].Sub[HIALARM].ID='F'; // A High Pressure alarm is identified by an upper-case 'R'

//-----------------------------------------

MenuItemsIdx++;

Menu[MenuItemsIdx].Text = "Pressure(S)"; // Create a menu item for the Secondary Pressure Transducer

Menu[MenuItemsIdx].Device = CanalPump;

Menu[MenuItemsIdx].Pin = A4; // Menu-item is for Pump-Option #0 (Canal) on Pin (A4)

Menu[MenuItemsIdx].ValueModifier = PRESSURE; // Modify value to display PSI instead of MPa

Menu[MenuItemsIdx].Sub[LOALARM].ID='s'; // A Low Pressure alarm is identified by a lower-case 's'

Menu[MenuItemsIdx].Sub[HIALARM].ID='S'; // A High Pressure alarm is identified by an upper-case 'S'

*/

//------------[ Start-Up the Display ( DO NOT CHANGE! )]-------------

for ( int i = 0; i <= MenuItemsIdx; i++ ) {

if ( Menu[i].Sub[LOALARM].ID != NULL || Menu[i].Sub[HIALARM].ID != NULL ) {

EEPROMGet(i); // Load Alarm values from EEPROM

}

}

GetItem(); // Get starting Menu item

LCD_display(); // Update the display

}

# 6.OPTIONAL ACCESSORIES

Optional Accessories can be added to the Ag-irrigation Remote Control system to enhance monitoring and control abilities.

## 6.1Hand-Remote

### 6.1.19V Rechargeable Batteries ( $18.90 )

It is highly recommended to purchase high output 300mAH or more rechargeable 9V Batteries; as the Hand-Remote will eat threw batteries pretty quickly.

At time of writing EBL 4x 600mAHh 9V Li-ion Rechargeable Batteries with Charger could be purchased for $18.90

http://www.ebay.com/itm/300974624904

NOTE: Even if a USB power is plugged in – If the power switch is turned ON it will still draw power from the battery. If you plug in USB for power be sure the power switch on the Hand-Remote unit is turned OFF.

## 6.2Pump-Controller

### 6.2.1Pressure

- Features
  - Offers a way to remotely monitor the water pressure
  - Default programming on pin A3

#### A.Materials ($9.59)

 5V 0-1.2 MPa Pressure Transducer Sensor Oil Fuel Diesel Gas Water Air Sensor Banggood.com (http://www.banggood.com/Pressure-Transducer-Sensor-Oil-Fuel-Diesel-Gas-Water-Air-Sensor-p-1007341.html) ( $9.59/EA ) |  (~30-feet) 4-lead outdoor wire required to reach from the pipe to the Pump-Controller ( See Outdoor Data Wire in BOM )

#### B.Installation

1. Remove the current Pressure Gauge from its location
2. Screw in the Pressure Transducer ( Typically does fit the same hole size and threads as the pressure gauge )
3. Wire up the Transducer as follows
  a. Transducer RED wire ( +5V ) → Cat5e ORANGE
  b. Transducer BLACK wire ( GND ) → Cat5e BROWN
  c. Transducer YELLOW wire ( SIGNAL ) → Cat5e BLUE
4. Wire the other end of the Cat5e Wire into the Pump-Controller
  a. Cat5e ORANGE → 5VDC
  b. Cat5e BROWN → GND
  c. Cat5e BLUE → A3



#### C.Firmware Adjustments

See #5.1.Adding Expansions|outline

To activate the Pressure Sensor on the Hand-Remote Unit

### 6.2.2Water Level

- Features
  - Offers a way to remotely monitor water-level in a ditch
  - Default programming on pins D4 (TRIG) and D5 (ECHO) – On Pump-Controllers Firmware

#### A.Materials ( $10.77/ea )

 (1) DC 5V Waterproof Ultrasonic Module Distance Measuring Transducer Sensor banggood.com (http://www.banggood.com/DC-5V-Waterproof-Ultrasonic-Module-Distance-Measuring-Transducer-Sensor-p-1094462.html) ( $ 10.77/EA ) |  (1) 4-PIN Female Dupont Header to connect to Circuit Board Pins ( See Dupont Headers in BOM ) |  (~30-feet) 4-lead outdoor wire required to reach from the ditch to the Pump-Controller ( See Outdoor Data Wire in BOM )

#### B.3D-Prints ( $1.30 )

- Print the Following Models on a 3D-Printer
  - Files Located at https://github.com/tgit23/AgIrrigationRemoteControl/tree/master/Accessories/Sonic%20Water%20Level%20Meter/3D-Prints-STL
  - Total Filament = 43.7 cm3 @ $0.03/cm3 ~ $1.30

 SonicCircuitBoardCase.stl ( 14.3 cm³ ⁾ |  SonicCableCover.stl ( 2.5 cm³ ⁾ |  SonicCircuitBoardCover.stl ( 6.7 cm³ ⁾
 SonicHeadCase.stl ( 17.6 cm³ ⁾ |  SonicHeadCover.stl ( 2.6 cm³ ⁾

#### C.Firmware Adjustments

See #5.1.Adding Expansions|outline

To activate the Ultrasonic Distance Water Level Meter on the Hand-Remote Unit

### 6.2.3Auxiliary Contact ( $43.75 )



- Auxiliary contact, side mounted, 1 N.O. Contact ( NOTE: This must match/fit the pump panels Contactor Unit )
  - https://www.automationdirect.com/adc/Shopping/Catalog/Motor_Controls/Eaton_Cutler-Hammer_Contactors_-z-_Starters_-z-_Overloads/Auxiliary_Contacts/C320KGS1 - $43.75/ea
- Notes
  - Auxiliary Contactor must be purchased according to the contactor they will FIT on.
    - The above suggested purchase will ONLY work with the NEMA-2 Model # AN16GNO Series B1 Contactor
  - The Auxiliary Contactor typically already used by the Start-lock CANNOT be used for this purpose as it has 480V wires already attached to it.
  - Often a used aux contactor can be found much cheaper on ebay
- Benefits
  - Offers a way to monitor the actual (i.e. directly) the pump power status

### 6.2.4Flow Meter

Did not implement due to high costs and limited benefits

http://www.banggood.com/TUF-2000M-TS-2-Digital-Ultrasonic-Flowmeter-Flow-Meter-Ultrasinic-Flow-ModuleRTU-p-1087832.html ( $186.77 )

# 7.TROUBLESHOOTING

- Support
  - You can email me at tgit28@gmail.com with any questions, comments and or requests. I'm glad to help in any way I can.
- Hand-Remote Problems
  - The Display is or started to show garbage
    - Typically this is a symptom of a low battery ( Replace the 9V Battery and see if that fixes the problem )
  - The Menu-Items all show 'ERR' ( Meaning it cannot communicate with the Pump-Controller )
    - 1) Unplug the Pump-Controller Box at the Pump-Panel Exit Plug
    - 2) Measure voltage across the two center pins; It should read approximately 24Vdc. If it doesn't --
      - Double check that the main breaker is ON
      - If the pins still do not read voltage; double check the installation steps ( Make sure to turn OFF the main breaker before opening the panel )
    - 3) If 24Vdc is measured at the Exit Plug ---
      - Remove the Pump-Controller cover
      - Measure voltage from the screw terminals labeled 5Vdc and GND; It should read approximately 5Vdc. If it doesn't --
        - Check that the DC power plug is plugged into the Arduino ( See BOM to determine which board is the Arduino )
        - Check that board lights are lit and one should be blinking
    - 4) If all the above is Okay
      - There may be a more serious problem like a solder joint has come UN-done or system configuration was lost.
      - You can try and re-configure the Xbee and Upload Firmware again; but the unit is deemed broken and should be returned for a replacement
- Pump-Controller Problems
  - The Pump doesn't turn ON although the Hand-Remote displays that Power is ON
    - 1) Be sure the Hand-Off-Auto Selector switch is set to Auto
    - 2) Double check the installation steps ( Make sure to turn OFF the main breaker before opening the panel )
      - Note: If the Solid State Relay was wired on the wrong side of the Start Button; this will cause a short when the Power was Set → ON on the Hand-Remote and the Solid State Relay may be fried and will need to be replaced.

# 8.OTHER RESOURCES / LINKS

- RF Controllers
  - Commercial
    - http://www.forbixindia.com/electronics/remote-motor-control/
    - http://www.remotecontroleverything.com/long-range-wireless-remote-control-3-phase-power-water-pump/
    - http://www.sprinklerwarehouse.com/remote-control-guide-s/6282.htm
    - http://www.sprinklerwarehouse.com/Hunter-Remote-Controllers-Timers-s/109.htm
    - http://rayshobby.net/opensprinkler/
    - Rain Bird Controller wiring diagram http://www.lawnh2o.com/rainbird/PDF/Wiring-Manual.pdf
  - Home-made Projects
    - https://www.instructables.com/id/COMPACT-AND-ROBUST-AUTOMATED-AGRICULTURE-REMOTE/
- Cellular Controllers
  - Commercial
    - http://www.myfieldnet.com/
    - https://www.ag-rite.com/system-description
    - 380V 50Hz 500W (TOO SMALL) https://www.alibaba.com/product-detail/GSM-industrial-three-phase-power-switch_60270579733.html ( $100-$200 )
    - Looks cheap http://www.bieneelectronics.com/products/br_application.htm
  - Home-made Projects
    - https://www.instructables.com/id/SMS-controlled-Wireless-Irrigation-System/
    - https://www.stavros.io/posts/arduino-powered-irrigation-system/
- Component considerations
  - Atmel328 with RF boards https://www.digitalsmarties.net/products/jeenode
  - ALL about Solid State Relays http://www.phidgets.com/docs/Solid_State_Relay_Primer
  - Remote Relay https://www.controlanything.com/Relay/Relay/XSC_PROXR
  - RF Remote http://www.remotecontroleverything.com/long-range-wireless-remote-control-3-phase-power-water-pump/ ( $83 – A serious alternative @ 2000-meter?? range )
- Digi Xbee Links
  - Sparkfun Xbee User Guide https://learn.adafruit.com/xbee-radios/
  - Sparkfun Xbee Buying Guide https://www.sparkfun.com/pages/xbee_guide
  - Xbee 1-WATT (up to 40-miles) https://www.digi.com/products/xbee-rf-solutions/embedded-rf-modules-modems/xtend-module#overview ( S3B is .25 Watts )
  - Xbee Homepage https://www.digi.com/products/xbee-rf-solutions

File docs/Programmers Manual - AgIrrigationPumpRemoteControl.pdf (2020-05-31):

# Ag Irrigation Remote Control

## Programmers Manual


By: TGIT-Tech
Visit my website at: http://www.tgit-tech.com/
Feel free to use: no strings attached (text content only / images respectfully referenced) Last Updated: 2020.05.24

# Table of Contents

1.2 About the Ag Irrigation Remote Control......3

3.1 Configuring Firmware for Xbee

( 1. INTRODUCTION :: INTRODUCTION :: INTRODUCTION ) Page -3-

### 1. INTRODUCTION

### 1.1 Whats Covered

✔ This booklet only needs to be read if:
◌ The project is built from scratch.
- Requiring firmware to be uploaded to both the Hand-Remote and Pump-Controller ◌ The current setup has changed
- Adding new accessories like a digital pressure meter or ultrasonic meter ( water-level ) requires firmware that reflects those additions
◌ Special operation is required
- Experienced programmers can program the units to operate however they wish

✔ This booklet is a guide for
◌ Configuring the Xbee RF Module
◌ Uploading Firmware onto the Hand-Remote and Pump-Controller's micro-controllers ◌ Details about customizing the firmware to match a users needs

### 1.2 About the Ag Irrigation Remote Control

The “Ag Irrigation Remote Control” project's goal is to provide RF ( Radio Frequency ) remote control and monitoring abilities to an Agriculture-Industrial 3-Phase 480VAC Irrigation Pump that is typically used in wheel-line and hand-line irrigation setups within the United States.

✔ The project implements
◌ Digi Xbee RF (https://www.digi.com/products/xbee-rf-solutions) radio modules ( S3B, 900MHz, 1/4-Watt ) which advertises a broadcast range of up to 28-miles ( Practical usage at 2-miles at ground level )
◌ Arduino micro-controller boards, LCD display shields, Zigbee shields, and various discrete devices

✔ The project consists of:
◌ Hand-Held “Hand Remote”
◌ Pole mounted “Pump Controller”
◌ High-Voltage Control “Installation Kit” which consists of components to be added to the pumps electrical panel

✔ The project is Open Source and its main page Resides at: https://github.com/TGit-Tech/AgIrrigationRemoteControl
◌ Releases ( All Finalized Plans, Files and Documentation ) can be downloaded at: https://github.com/TGit-Tech/AgIrrigationRemoteControl/releases
◌ The online manual can be seen at: https://tgit-tech.github.io/AgIrrigationRemoteControl/manual/

( 2. Uploading Firmware :: Uploading Firmware :: Uploading Firmware ) Page -4-

### 2. Uploading Firmware

1. Install Arduino Sketch IDE
a) In a web-browser; go to https://www.arduino.cc/en/Main/Software
b) Scroll down to 'Download the Arduino IDE' and Select the Windows Installer
c) Save Install file to a place you'll remember – like Documents or Desktop
d) Run the saved filed to Install the Arduino Sketch IDE.


2. Install the PEERIOSERIALCONTROL Library
a) In a web-browser; go to https://github.com/TGit-Tech/PeerIOSerialControl/releases
b) Under LATEST RELEASE D → OWNLOADS click on SOURCE CODE (ZIP)
c) Save to a place you'll remember – like Documents or Desktop
d) Run the Arduino Sketch IDE installed in Step #1
e) Choose Menu Item SKETCH → INCLUDE LIBRARY → ADD .ZIP LIBRARY
f) Select the PEERIOSERIALCONTROL.ZIP Library file saved in step 'c' above


3. Install the SSOFTWARESERIAL Library - Required by the Hand-Remote Firmware
a) In a web-browser; go to https://github.com/TGit-Tech/SSoftwareSerial/releases
b) Under LATEST RELEASE D → OWNLOADS click on SOURCE CODE (ZIP)
c) Save to a place you'll remember – like Documents or Desktop
d) Run the Arduino Sketch IDE installed in Step #1
e) Choose Menu Item SKETCH I → NCLUDE LIBRARY → ADD .ZIP LIBRARY
f) Select the SSOFTWARESERIAL.ZIP Library file saved in step 'c' above

( 2. Uploading Firmware :: Uploading Firmware :: Uploading Firmware ) Page -5-

4. Download the Firmware
a) In a web-browser; go to https://github.com/TGit-Tech/AgIrrigationRemoteControl/releases
b) Under LATEST RELEASE D → OWNLOADS click on SOURCE CODE (ZIP)
c) Save to a place you'll remember – like Documents or Desktop
d) Unzip the Folder
e) In Arduino Sketch IDE choose FILE → OPEN and Select
- File HANDREMOTE.INO for the HANDREMOTE Firmware
- ~\AgIrrigationRemoteControl-master\AgIrrigationRemoteControl-master\HandRemote
- File PUMPCONTROLLER.INO for the PUMPCONTROLLER Firmware
- ~\AgIrrigationRemoteControl-master\AgIrrigationRemoteControl-master\PumpController\PumpRemote


( 2. Uploading Firmware :: Uploading Firmware :: Uploading Firmware ) Page -6-

5. Compile and Upload the Firmware
a) Plug in a USB cable from the Computer to the unit
b) Select the Port the units USB is connected to; in Sketch menu TOOLS → PORT
- To determine Port; Open Windows Device Manager Ports ( COM & LPT ) a new COM?? → port appears right after plugging in the cable
c) Select the Board; Sketch menu TOOLS → BOARD → ARDUINO/GENUINO UNO
d) In Arduino Sketch IDE; Press the Right-Arrow next to the Check mark in the Top-Left Corner to upload the firmware onto the unit

( 2.1 Uploading Firmware :: Adding Expansions :: Adding Expansions ) Page -7-

### 2.1 Adding Expansions

1. Follow the steps in 2.Uploading Firmware to Step #4 for the Hand-Remote firmware; Hold off on Step #5; “Compile & Upload”
2. Once the file is open in Arduino Sketch IDE; locate the following code-block which should be right at the top

//=================================================================================================== //------------------------------ SIMPLE USER CONFIGURATION SETTINGS ---------------------------------//===================================================================================================
#define BUILD_VERSION | 20170622 // Release Version used to Build the Unit

( without the dots )
#define TRANSCEIVER_ID | 1 | // Unique numeric (ID)entity for this Unit(1-15)

#define XBEECONFIG | 0 | // 0 = RUN, 1 = Configure the XBEE using XCTU

#define ULTRASONIC_WATER_LEVEL_INSTALLED 0 | // 0 = NO, 1 = YES ( Wire TRIG -> D4, ECHO -> D5 )

#define WATER_PRESSURE_INSTALLED | 0 | // 0 = NO, 1 = YES ( Wire SENSE -> A3 )

//^^^[ END - SIMPLE USER CONFIGURATION SETTINGS ] ^^^^^^^^^^^^^^^^^^^^^^^^^^^^^^^^^^^^^^^^^^^^^^^^^^^^^^^^^^^^^^^^^^^^^^

3. As described within the comments ( text following '//' )
a) Change ULTRASONIC_WATER_LEVEL_INSTALLED to a '1' for water-level sensor ability.
b) Change WATER_PRESSURE_INSTALLED to '1' for pressure sensor ability.
c) Then proceed to Step #5 in 2.Uploading Firmware and Compile & Upload the changes just made

### 3. Xbee RF Configuration

The XBEE RF Module is setup from the factory to work without any additional changes. However, often it is very wise to assign non-factory setting in order to keep your RF communications from being interfered with by other XBEE devices in the neighborhood. Changes to the ID NETWORK ID
( described below ) will need to be preformed on all HAND-REMOTES and all PUMP-CONTROLLERS

Generally, Digi XCTU will work with Pump-Controllers but occasionally there seems to be some issue with XCTU communicating with the Xbee modules on the Hand-Remotes. If XCTU cannot communicate properly with the Xbee module use section 3.3.Configuring Xbee using Putty as an alternative.

### 3.1 Configuring Firmware for Xbee Configuration Changes

1. Upload Firmware with XBEE Configuration Set
a) To change the XBEE settings – Follow Steps #1 to #3 in 2.Uploading Firmware

With the Firmware file open find the following line of code; which should be very close to the top
#define XBEECONFIG | 0 | // 0 = RUN, 1 = Configure the XBEE using XCTU

Change it to
#define XBEECONFIG | 0 | // 0 = RUN, 1 = Configure the XBEE using XCTU

b) Proceed to upload the firmware to the Unit as outline in Step #4 in 2.Uploading Firmware

### 3.2 Configuring Xbee using Digi XCTU

2. Install Digi-XCTU

( 3.2 Xbee RF Configuration :: Configuring Xbee using Digi XCTU :: Configuring Xbee using Digi XCTU ) Page -8-

a) The Digi XCTU software can be gotten from https://www.digi.com/products/xbee-rf-solutions/xctu-software/xctu (https://www.digi.com/products/xbee-rf-solutions/xctu-software/xctu)
3. Run Digi-XCTU


a) Click + ( Add Radio ) mark in the top left corner and enter the unit's COM port ( Arduino )
b) The main values that may be of interest are:
- ID Network ID | - This sets a unique private “Channel” (Must be same on all units)
- PL TX Power Level | - If devices are close; a lower power setting can preserve battery life
4. Save Settings to the Xbee and Reload Firmware
a) Be sure to click the “Write” button in XCTU to save any settings that were made
b) Close XCTU
c) In Arduino Sketch IDE restore the following line to its original
#define XBEECONFIG | 0 | // 0 = RUN, 1 = Configure the XBEE using XCTU

d) Upload the firmware to the Unit as outline in Step #4 in 2.Uploading Firmware

### 3.3 Configuring Xbee using Putty

1. Install Putty
◌ Software can be gotten at https://putty.org/
2. Setup Putty
◌ Under CATEGORY | C → ONNECTION | S → ERIAL check the following settings

( 3.3 Xbee RF Configuration :: Configuring Xbee using Putty :: Configuring Xbee using Putty ) Page -9-


◌ Under SESSION enter the COMxx Port of the Hand-Remote or Pump-Controller, set Speed at 9600 and Connection Type SERIAL


◌ Then click OPEN to open a Terminal Window

3. Make Xbee Settings in the Terminal Window
◌ Press '+++' without hitting enter. Xbee should respond with an 'OK'. You're now in 'AT' Command mode.
◌ Type 'ATID' and hit enter. Xbee will respond with the current Xbee Network ID set on the Xbee Module ( i.e. 'AT' – 'ID' )
◌ Xbee will escape its 'settings' mode quickly so if it was responding but isn't anymore; enter the '+++' to enter settings mode again.
◌ Use command 'ATWR' to write the settings to the Xbee Module permanently
◌ Example below shows how one would setup the Xbee with Network ID 1200
- '+++' | (no enter) | Xbee Responds with 'OK'
- ATID 1200 | (enter) | Xbee Responds with 'OK'
- ATID | (enter) | Xbee Responds with '1200' the setting just made
- ATAP 0 | (enter) | This sets Xbee in 'Transparent Mode'
- ATWR | (enter) | This permanently stores the above settings

( 3.3 Xbee RF Configuration :: Configuring Xbee using Putty :: Configuring Xbee using Putty ) Page -10-

◌ For a full list of settings see the “Command Reference Table” in
- Location https://www.digi.com/products/xbee-rf-solutions/sub-1-ghz-modules/xbee-pro-xsc#productsupport (https://www.digi.com/products/xbee-rf-solutions/sub-1-ghz-modules/xbee-pro-xsc#productsupport)
- In PDF https://www.digi.com/resources/documentation/digidocs/pdfs/90002173.pdf

( 4. Customizing Firmware :: Customizing Firmware :: Customizing Firmware ) Page -11-

### 4. Customizing Firmware

### 4.1 Pump-Controller

✔ The Pump-Controller Firmware preforms the following duties
◌ Wait for Hand-Remote Requests and generate responses
◌ Calculate values ( Virtual-Pin Values ) for special devices that require a process to obtain a value ( like ping/echo for Ultrasonic level measurements )
◌ Retain a Power-Off status after a power failure has occurred at the pump ( Arduino is designed to keep digital pins low after a power failure )

NOTE: Wiring, Timing, and Almost all system functions are implemented on the HAND-REMOTE Firmware

### 4.1.1 Virtual Pins

Virtual pins are non-hardware related value identifiers that are created and assigned by the PUMP-CONTROLLER firmware and then accessed by the HAND-REMOTE as a “Pin” value. An example case is the ultrasonic water level; The pump-controller firmware pings and times an echo of the ultrasonic distance meter using its D4 ( Trigger ) and D5 ( Echo ) pins and stores the measured value on “virtual pin 64”. When the Hand-Remote queries for a value on pin-64 it actually gets the measured value which is a combination of D4 & D5 already calculated by the PUMP-CONTROLLER.

✔ An Example of a Virtual Pin setup on the PUMP-CONTROLLER firmware
void loop(){

XBee.Available();

#if US_PRESENT>0

// Read UltraSonic water level
int ulCurrentTime = millis();
if ( ulCurrentTime > ulLastPing + 1000 ) {
| XBee.VirtualPin(64, sonar.ping_in() );
ulLastPing = ulCurrentTime;
}
#endif

}

### 4.2 Hand-Remote

✔ The Hand-Remote Firmware preforms the following duties

◌ Storing the alarm values in non-volatile memory (EEPROM) so user values and settings aren't lost every-time the power is turned off
◌ Updating the current status (MAIN Values) of the Menu-Items and checking for Alarm boundaries.

( 4.2 Customizing Firmware :: Hand-Remote :: Hand-Remote ) Page -12-

◌ Processes User Input
- UP/DOWN user buttons will increments or decrements the Menu-Items
- RIGHT/LEFT user buttons will increments or decrements the Sub-Function of each Menu-Item
- ENTER ( square ) user button will preform a value SET; or update MAIN values when they are being displayed

◌ Menu-Items are associated/connected to a Device and its Hardware Pin
- Device | - Example; The Hand-Remote running this firmware, or a
Pump-Controller device controlling a pump
- Pin | - Example; 7(for D7) or A2 as identified inside the Pump-
Controller Unit or by the Arduino UNO board

◌ Menu-Items have Sub[?] Values, such as
- The actual/read/MAIN value of the Menu-Items - Example; Power is currently either ON/OFF ( current status )
- SETting a Value for the Menu-Item | - Example; SET the Power to
either ON/OFF
- Setting a Too LOw ALARM Value | - Example; When pressure is
below 10 sound the Low Alarm
- Setting a Too HIgh ALARM Value | - Example; When pressure is
above 100; sound the High Alarm

◌ Menu-Items can have Option Values ( An Optional way of handling Menu-Item value assignments )
- Options associates a common MAIN-Value to a Text identifier; for example ON/OFF.
- A Menu-Items value must be a select-able set of Options or a Number but cannot be both.
- The maximum number of options is limited by program line #define MAXOPTIONS 2
// Maximum number of Menu Item Options allowed

◌ Menu-Item Limits
- Program line #define MAX_MENU_ITEMS 15 | // Maximum number of Menu
Items allowed ( using 71% dynamic memory )
- Determines the maximum number of menu-items that can exist; it can be increased slightly but may produce memory warnings.

### 4.2.1 Adding & Deleting Devices

✔ The Hand-Remote Firmware tracks ALL the associated devices it can control and monitor.

◌ To add another Device to the control and monitoring system
- Add any Unique Name to the Comma separated list of devices on the Program Line shown below
- uDevices HandRemote, CanalPump, DitchPump; // Name and Define all controllable devices in the System
- At the top of the SetupMenu() function; Assign the Unique Named device a .Text Identifier ( Used in the Menu )
- At the top of the SetupMenu() function; Assign the Unique Named unit Unit's .Transceiver_ID number assigned in the units firmware
- Example Program Line CanalPump.Text = "Canal Pump"; CanalPump.TransceiverID

( 4.2.1 Customizing Firmware :: Hand-Remote :: Adding & Deleting Devices ) Page -13-

= 10;
◌ Delete devices by removing the items in the adding devices listed above.
- Note: If there is no conflict of Transceiver_ID's or naming there really isn't a substantial need to remove a “missing” device from the system.

### 4.2.2 Creating a Menu-Item

1. Find the SetupMenu() function in the Hand-Remote firmware file; This is where all the Menu-Items are defined
2. Indexing - Determine where in the list of Menu-Items you'd like the new item to appear
a) All Items MUST BEGIN with line MenuItemsIdx++; except the very first item ( Usually the Hand-Remote battery status )
b) The line above increments the Indexing ( line count ) to allow the new menu-item to exist
c) Items that do not have [MenuItemsIdx] indexing are used in other places of the firmware and should NEVER BE CHANGED!
3. Device - Assign the device this Menu-Item is attached to
a) This is the Device's Unique Name given in Step #A|Adding & Deleting Devices
b) The unit is generally a named Pump-Controller device with an assigned Transceiver_ID.
4. Pin – Assign the Hardware Pin of the device that the Menu-Item will control or monitor
a) The hardware pin is the terminal inside the controlling device box ( pump-controller ) that the control/monitor equipment is wired to
b) NOTE: Digital Pins ( D4 D7 ) are identified by only their number ( e.g. 4 = D4 ) → whereas Analog pins require both letter and number ( e.g. A2 ).
- Digital Example; | Menu[MenuItemsIdx].Pin=7;
- Analog Example; | Menu[MenuItemsIdx].Pin=A3;
5. Text - Assign the Menu-Item a defining Text
a) The text is what will be displayed on the Hand-Remote display
- Example; Menu[MenuItemsIdx].Text=”Power”;
6. Options - Determine IF the Menu-Item will have textual “Options” or is just a numerical value
a) If the Menu-Item will report numerical values such as Voltage, Water Level, Pressure etc... Skip to step #5
b) Determine the Menu-Items Options and assign each a;
- Text | Example; Menu[MenuItemsIdx].Option[0].Text = “On”;
- Value | Example; Menu[MenuItemsIdx].Option[0].Value = HIGH;
7. Sub[SET] – Determine IF the user should be allowed to set a value on the Location ( Output Pins like turning Power ON/OFF )
a) If the Menu-Item is for monitoring status and the user will not be setting its value (INPUT)... Skip to step #7
b) If the Menu-Item needs to allow the user the ability to set the value ( OUTPUT )
- Set the “State” to SETTABLE to allow the user to SET the value
- Example; Menu[5].Sub[SET].State = SETTABLE;

( 4.2.2 Customizing Firmware :: Hand-Remote :: Creating a Menu-Item ) Page -14-

8. Sub[??ALARM] – Determine if the value should be monitored with an alarm
a) LOALARM
- If the Menu-items value is numeric and the value should be checked for getting too small
- OR If the Menu-item value is an “option” and the value should be checked to see if it is EQUAL
- Assign an LOALARM identifier | Example; Menu[5].Sub[LOALARM].ID =
'c';
b) HIALARM
- If the Menu-items value is numeric and the value should be checked for getting too large
- OR If the Menu-Item value is an “option” and the value should be checked to see if it is NOT-EQUAL
- Assign a HIALARM identifier | Example; Menu[5].Sub[HIALARM].ID =
'C';
9. Proceed to #4.3.2.3.Updating Changes|outline

### 4.2.3 Deleting a Menu-Item

1. Find the menu item you'd like to delete by identifying it by its' Menu[MenuItemIdx].Text setting
2. Select ALL the items from MenuItemsIdx++; up to but no including the next MenuItemsIdx++;
3. Press delete
A. Menu-Item Setup ( Example )
The menu items are defined in the SetupMenu() Function identified by line 'void SetupMenu() {'. Each item in the Menu has a numeric index (i.e. Menu[index-#] below the constant 'MONITOR' is assigned index-0 and 'PUMPIDX' is assigned index-1).

//==================================================================================================== //------------------------------ MENU STRUCTURE ( ADVANCED CONFIGURATION ) ---------------------------//==================================================================================================== //**************************************************************************************************// **
* @brief Setup the LCD menu
* @remarks
* - Allows a single spot customization to the user interface
* - Display will show the items in the same order as they are defined here * @code
* exmaple code
* @endcode
*****************************************************************************************************/ uDevices HandRemote, CanalPump, DitchPump; // Name and Define all controllable devices
void SetupMenu() {

HandRemote.Text = "Hand Remote"; HandRemote.TransceiverID = TRANSCEIVER_ID;
DitchPump.Text = "Ditch Pump"; DitchPump.TransceiverID = 10;
CanalPump.Text = "Canal Pump"; CanalPump.TransceiverID = 11;

//BATT (idx-0) ----------------------------
Menu[BATT].Device = HandRemote;
Menu[BATT].Pin = A1; // Battery level from the Hand-Remote pin A1 Menu[BATT].Text = "Battery(B)"; // Create a menu item for monitoring the Battery Menu[BATT].ValueModifier = BATTVOLTS; // Modify raw value to show voltage Menu[BATT].Sub[LOALARM].ID = 'b'; // A Low Alarm is identified by a lower-case 'b'

//-----------------------------------------
MenuItemsIdx++;
idx = MenuItemsIdx; // !!!-- Set where the Menu will start --!!!

( 4.2.3 Customizing Firmware :: Hand-Remote :: Deleting a Menu-Item ) Page -15-

Menu[MenuItemsIdx].Device = DitchPump;
Menu[MenuItemsIdx].Pin = 7; // Power is on all Pump-Controller's on pin [D7] Menu[MenuItemsIdx].Text = "Power(P)"; // Create a menu item for Power Control Menu[MenuItemsIdx].Sub[SET].State = SETTABLE; // Allow this Value to be 'SET' by the user Menu[MenuItemsIdx].Sub[LOALARM].ID = 'p'; // A Low Alarm is identified by a lower-case 'p' Menu[MenuItemsIdx].Sub[HIALARM].ID = 'P'; // A High Alarm is identified by an upper-case 'P' Menu[MenuItemsIdx].Option[0].Text = "Off"; // Power can be "Off" - Option #0 = Off Menu[MenuItemsIdx].Option[0].Value = LOW; // "Off" will be the value 'LOW" - Off = LOW Menu[MenuItemsIdx].Option[1].Text = "On"; // Power can be "On" - Option #1 = On Menu[MenuItemsIdx].Option[1].Value = HIGH; // "On" will be the value 'HIGH' - On = HIGH
Menu[MenuItemsIdx].LastOptionIdx = 1; | // Last Option Index defined (Number of Options - 1)

//-----------------------------------------
#if ULTRASONIC_WATER_LEVEL_INSTALLED>0

MenuItemsIdx++;
Menu[MenuItemsIdx].Device = DitchPump;
Menu[MenuItemsIdx].Pin = 64; // Water Level from VIRTUAL (Pump-Controller) Menu[MenuItemsIdx].Text = "Water (L)"; // Create a menu item for Water Level Transducer Menu[MenuItemsIdx].Sub[LOALARM].ID = 'l'; // A Low Alarm is identified by a lower-case 'l' Menu[MenuItemsIdx].Sub[HIALARM].ID = 'L'; // A High Alarm is identified by an upper-cse 'L' #endif
//-----------------------------------------
#if WATER_PRESSURE_INSTALLED>0

MenuItemsIdx++;
Menu[MenuItemsIdx].Device = DitchPump;
Menu[MenuItemsIdx].Pin = A3; // The 'signal' is on Pump-Controllers on pin [A3] Menu[MenuItemsIdx].Text = "Pressure(R)"; // Create a menu item for the Primary Pressure Menu[MenuItemsIdx].ValueModifier = PRESSURE; // Modify value to display PSI instead of MPa Menu[MenuItemsIdx].Sub[LOALARM].ID='r'; // Low Pressure alarm is identified lower-case 'r' Menu[MenuItemsIdx].Sub[HIALARM].ID='R'; // High Pressure alarm is identified upper-case 'R' #endif
/*// UN-COMMENT BELOW FOR A SECOND PUMP-CONTROLLER ( NAMED "Canal Pump" ) WITH TRANSCEIVER_ID = 11 //-----------------------------------------
MenuItemsIdx++;
Menu[MenuItemsIdx].Text = "Power(C)"; // Create a menu item for Power Control Menu[MenuItemsIdx].Device = CanalPump;
Menu[MenuItemsIdx].Pin = 7; // Power is on all Pump-Controller's on pin [D7] Menu[MenuItemsIdx].Sub[SET].State = SETTABLE; // Allow this Value to be 'SET' by the user Menu[MenuItemsIdx].Sub[LOALARM].ID = 'c'; // A Low Alarm is identified by a lower-case 'p' Menu[MenuItemsIdx].Sub[HIALARM].ID = 'C'; // A High Alarm is identified by an upper-case 'P' Menu[MenuItemsIdx].Option[0].Text = "Off"; // Power can be "Off" - Option #0 = Off Menu[MenuItemsIdx].Option[0].Value = LOW; // "Off" will be the value 'LOW" - Off = LOW Menu[MenuItemsIdx].Option[1].Text = "On"; // Power can be "On" - Option #1 = On Menu[MenuItemsIdx].Option[1].Value = HIGH; // "On" will be the value 'HIGH' - On = HIGH
Menu[MenuItemsIdx].LastOptionIdx = 1; | // Last Option Index defined (Number of Options - 1)

//-----------------------------------------
MenuItemsIdx++;
Menu[MenuItemsIdx].Text = "Pressure(F)"; // menu item for the Primary Pressure Transducer Menu[MenuItemsIdx].Device = CanalPump;
Menu[MenuItemsIdx].Pin = A3; // 'signal' is gotten Pump-Controllers on pin [A3] Menu[MenuItemsIdx].ValueModifier = PRESSURE; // Modify value to display PSI instead of MPa Menu[MenuItemsIdx].Sub[LOALARM].ID='f'; // Low Pressure alarm is lower-case 'r' Menu[MenuItemsIdx].Sub[HIALARM].ID='F'; // High Pressure alarm is upper-case 'R'

//-----------------------------------------
MenuItemsIdx++;
Menu[MenuItemsIdx].Text = "Pressure(S)"; // menu item for the Secondary Pressure Transducer Menu[MenuItemsIdx].Device = CanalPump;
Menu[MenuItemsIdx].Pin = A4; // Menu-item is Pump-Option #0 (Canal) on Pin (A4) Menu[MenuItemsIdx].ValueModifier = PRESSURE; // Modify value to display PSI instead of MPa Menu[MenuItemsIdx].Sub[LOALARM].ID='s'; // Low Pressure alarm is lower-case 's' Menu[MenuItemsIdx].Sub[HIALARM].ID='S'; // High Pressure alarm is upper-case 'S'
*/
//------------[ Start-Up the Display ( DO NOT CHANGE! )]-------------
for ( int i = 0; i <= MenuItemsIdx; i++ ) {
if ( Menu[i].Sub[LOALARM].ID != NULL || Menu[i].Sub[HIALARM].ID != NULL ) { EEPROMGet(i); // Load Alarm values from EEPROM }
}
GetItem(); // Get starting Menu item LCD_display(); // Update the display }

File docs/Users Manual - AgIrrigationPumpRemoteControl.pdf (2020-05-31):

# Ag Irrigation Remote Control

## Users Manual


By: TGIT-Tech
Visit my website at: http://www.tgit-tech.com/
Feel free to use: no strings attached (text content only / images respectfully referenced) Last Updated: 2020.05.24

# Table of Contents

4.1.1 9V Rechargeable Batteries ( $18.90 )16

( 1. INTRODUCTION :: INTRODUCTION :: INTRODUCTION ) Page -3-

### 1. INTRODUCTION

The “Ag Irrigation Remote Control” project's goal is to provide RF ( Radio Frequency ) remote control and monitoring abilities to an Agriculture-Industrial 3-Phase 480VAC Irrigation Pump that is typically used in wheel-line and hand-line irrigation setups within the United States.

✔ The project implements
◌ Digi Xbee RF (https://www.digi.com/products/xbee-rf-solutions) radio modules ( S3B, 900MHz, 1/4-Watt ) which advertises a broadcast range of up to 28-miles ( Practical usage at 2-miles at ground level )
◌ Arduino micro-controller boards, LCD display shields, Zigbee shields, and various discrete devices

✔ The project consists of:
◌ Hand-Held “Hand Remote”
◌ Pole mounted “Pump Controller”
◌ High-Voltage Control “Installation Kit” which consists of components to be added to the pumps electrical panel

✔ The project is Open Source and its main page Resides at: https://github.com/tgit23/AgIrrigationRemoteControl
◌ Releases ( All Finalized Plans, Files and Documentation ) can be downloaded at: https://github.com/tgit23/AgIrrigationRemoteControl/releases
◌ This document ( most recent version ) can be seen at: https://tgit23.github.io/AgIrrigationRemoteControl/AgIrrigationPumpRemoteControl.pdf ◌ Pre-Built Purchasing options are available – See the projects main page link above
A. Signal Strength ( 2-Miles )

✔ Standard Signal distance is recommended for usage of up to 2-miles

◌ Elevated or higher gain antennas can be purchased to extend this range

◌ Test Scenario
- Pump-Controller mounted 5-feet from the ground on the power pole next to the pump
- Hand-Controller checked inside a moving vehicle ( ~ 3-feet off the ground )

◌ Test Environment
- Houses located on square mile blocks; each mile having approximately 6 to 10 houses per mile
- Ground level is fairly flat

◌ Results
- < 1-mile - Coverage approximately 99% of spot locations ( very few spots inside a house will loose signal )
- 1-to-2 miles - Coverage approximately 90% of spot locations ( a few spots inside a vehicle will loose signal )
- 2-to-3 miles - Coverage approximately 5% of spot locations ( very few spots get a signal )
- 3-to-4 miles - A few signals were obtained at up to 3-3/4 miles away; but spot

( 1. INTRODUCTION :: INTRODUCTION :: INTRODUCTION ) Page -4-

location was very very temperamental.

B. Features

✔ A solid rural 2-Mile range
✔ No cellular, FCC licensing or other requirements are needed; Just hook it up and use it
✔ A single Hand-Remote can control multiple irrigation pumps
✔ Multiple Hand-Remotes can control the same irrigation pump
✔ Uses the Pump Panels “AUTO” selection; so it doesn't disturb manual operation of Hand-Off & Start sequences
✔ Implements a “Stay-Off” after power losses that is required by power companies
✔ Easily expandable to offer Pressure and Water-Level monitoring
✔ Built upon mass-produced development boards that can be easily purchased and replaced

✔ Hand-Remote settable Alarms ( buzzer ) to notify user of
◌ Power changes | - For Example; Alarms when pump
shuts down due to a power loss
◌ Water Pressure boundaries ( if equipped ) - For Example; Alarms when pressure drops due to a hose that has fallen off or broken pipe
◌ Ditch Water-Level boundaries ( if equipped ) - For Example; Alarms when water in the ditch is too low or too high

### 2. INSTALLATION INSTRUCTIONS

This section is a guide to installing the PUMP-CONTROLLER using the INSTALLATION KIT. If these products were not purchased they can be built by following the “Building Instructions” booklet.


( 2. INSTALLATION INSTRUCTIONS :: INSTALLATION INSTRUCTIONS :: INSTALLATION INSTRUCTIONS )

✔ Installation will require the following SUPPLIES

◌ Pump-Controller
- The white box shown on the right in the picture above
- Including the attached Antenna, Cable and 4-pin plug ending

◌ Installation Kit ( Including the following items )
- A 3-Phase Power Supply attached to a DIN rail
- 480VAC Input to 24Vdc Output
- A Solid State Relay (SSR) attached to a DIN rail
- 480VAC ( or higher ) Load Voltage and 5Vdc Input
- 12-feet of RED 600V 16-Gauge or heavier THHN or MTW wire
- 4-feet of GREEN 600V 16-Gauge or heavier THHN or MTW wire
- A Pump-Panel Exit Cable
- A 4-pin plug ending attached to (3) 4ft 600V rated wires
- Yellow plug wire Orange Hookup wire (+Vdc) →
- Black plug wire Brown Hookup wire (-Vdc) →
- White plug wire Blue Hookup wire (SSR-Control) →
- Green plug wire Unused ( None ) →
- (2) #8-32 x 1/2” Machine Screws
- (1) Wood screw for mounting the PUMP-CONTROLLER to a pole

✔ Installation will require the following TOOLS
◌ Personal protective gear ( e.g. insulated/flash protection clothing ) ◌ Voltmeter - that reads up to or beyond 500VAC
◌ Cordless drill
◌ Wire strippers and cutters
◌ #1 Phillips and #1 Flat head screw drivers
◌ Center Punch
◌ #29 ( 9/64” ) Drill Bit
◌ #8-32 Threading tap
A. Electrical Panel Introduction

Read through the following section to gain general knowledge on the items within the pumps electrical panel.

Most 3-phase irrigation pumps that do not have variable frequency drives(VFD) or inverters are setup similarly. Below is the details of a pumps electrical panels as an example or reference to the pumps power circuit. This information was gathered to determine the wiring and power needed to control the pumps power.


✔ Wiring Diagram Description
◌ L1, L2, L3 - Are the three HOT wires of the 3-Phase Power ( 480VAC ) going through the main breaker
◌ M | - The Starter Contactor ( example picture below ) contains:
- Activation Coil - Represented by the M-Circle in the wiring diagram just right of the Start Button ( this Activates the “Hammer” Switch )
- The Activation Coil resides “inside” the “Starter Contactor” Assembly; but can be
| removed by disassembling the unit.
- Main Contacts - The M-Contacts (-||-) that connects the L1,L2,L3 lines OL →
( Overloads ) Motor ( Sometimes called the “Hammer” ) →
- The Main Contacts are significant part of the “Starter Contactor” as a whole unit.


- Hold Contact - Represented by the M-Contact (-||-) wired in parallel and just below the Start Button
- The Hold Contact “LOCKS” the Activation coil ON when the Start-Button is pressed.
- The Hold ( sometimes referred to as an Auxiliary Contact ) clamps onto the side of the “Starter Contactor”
- As shown in picture above as the clamped on the right unit with a Grey square center.

◌ Hand, Off, Auto Switch
- In the wiring diagram above; the Hand-Off-Auto selector switch is in the “Auto” position where it is then connected to a Pressure Switch
- The Solid State Relay, that is part of the Installation kit, will be attached where this “Pressure Switch” is shown in the diagram.


✔ Description of Operation

When HAND is selected the “control circuit” ( L1 L2 loop ) is still open until the Start → Button is pressed. When the Start button is pressed it activates the (M) Activation Coil which in-turn activates the “Hold Contact” ( the --| |-- in parallel to the Start Button). This right-side contactor holds the “control circuit” closed until there is a power failure bump or the Hand-Off-Auto Switch breaks open the circuit loading the (M) activation coil.

This Projects SSR-Relay will be connected where the “Pressure Switch” is shown in this wiring diagram and will use the AUTO switch selection. This setup will require that the Arduino NOT re-activate power after a power failure has occurred until a specified time delay or turned back on. The click in HAND circuit is setup so the power company can re-activate power after a power failure without the over-load of all motors kicking on at the same time.

✔ Checking Amperage Limitations
◌ Activation Coil Amperage can be gotten by looking up the “Starter Contactor” specification sheet, for example;
- See Page 9 “AC COIL DATA” for NEMA Size #2 Shows 230VA(Volt-amperes which is VA=V*A) so 230VA/480Vac = 0.479Amps @ 480V
- The Solid State Relay in the Installation Kit can supply up to 10A; So it is well equipped to handle much larger Starter Contractors.

✔ Links to more information
◌ http://www.eaton.com/ecm/idcplgIdcService=GET_FILE&allowInterrupt=1&RevisionSelectionMethod=LatestReleased&noSaveAs=0&Rendition=Primary&dDocName=9980562 82226 (http://www.eaton.com/ecm/idcplgIdcService=GET_FILE&allowInterrupt=1&RevisionSelectionMethod=LatestReleased&noSaveAs=0&Rendition=Primary&dDocName=998056282226)
◌ http://www.eaton.com/Eaton/ProductsServices/Electrical/ProductsandServices/AutomationandControl/EnclosedControl/NEMA/PumpPanels/index.htm (http://www.eaton.com/Eaton/ProductsServices/Electrical/ProductsandServices/AutomationandControl/EnclosedControl/NEMA/PumpPanels/index.htm)
B. DIN-Rail Mounting

BE SURE THE MAIN BREAKER IS TURNED OFF AND CAREFULLY CHECK THAT THERE IS NO VOLTAGE ON THE OUTPUT OF THE MAIN BREAKER WITH A PROPER METER!!! 480VAC is deadly; and can cause severe flash burn and/or death. (e.g. A meter on the wrong setting can “flash” explode causing “flash” burns on you even at a distance away). I DISCLAIM ANY AND ALL RESPONSIBLITY FOR ANY RISKS, HARMS, INJURIES OR PROPERTY DAMAGE THAT WAS A RESULT OF FOLLOWING ANY INSTRUCTION IN THIS MANUAL.
See https://www.youtube.com/watch?v=6hpE5LYj-CY
1. Check your volt meter
a) Before leaving to install; check that your volt meter is working by plugging it into a household outlet ( Use the same setting >500 VAC )
b) Make sure the probes are plugged into their correct spots on the meter
c) Do not make any more changes to the volt meter after testing its correct operation.
2. Follow safe practices
a) Never turn ON the main breaker with the panel open
b) Never stand in front of the panel while turning on the main breaker ( flash explodes will often blow the front panel clear off ) - stand at the side
c) Never work in the same side of the box where the live wires ( feed wires ) exist – generally at the top of the box
d) Always stand as far away as you can
3. Prepare for Installation
a) Switch the Main Breaker to OFF from the outside of the pumps electrical panel
b) Open the pumps electrical panel
c) Double check your voltmeter setting – Never measure for 480VAC with a lower setting; it will cause many meters to flash explode
d) With leather gloves on, very carefully making sure not to wiggle the probes out of place, measure the following voltages
- From the bottom of the Main Breaker; Measure voltage between each of the 3-connectors ( They should all be 0V)
- From the bottom of the Main Breaker; Measure voltage between each of the 3-connectors and the ground metal of the electrical panel ( 0V )
4. Plan a location inside the Electrical Panel for the Power Supply and SSR mounted on the DIN rail
a) Requires approximately a 6” Wide x 6” Tall x 6 1/2” Deep envelope
b) Find a location as far away from other hot wires as possible ( eliminate the risk of a loosened wires falling and touching a low-voltage wire )
a) Preferably a location at the bottom of the box where the exit plug can quickly drop out of the box.
5. Mount the DIN Rail
a) Hold the DIN Rail in the desired location and punch the metal through easily accessible mounting slots in the DIN Rail on both ends
b) Drill two holes in the punch markings ( Bit Size #29 – 9/64” - 0.1360” )
c) Tap-thread the two holes just drilled ( #8-32 threading tap )
d) Hold the DIN rail in place and fasten it with (2) #8-32 machine screws

6. Attach ( If taken off ) the Power Supply and Solid State Relay to the DIN Rail


Illustration 1: Note; the Fulree Converter pictured IS NO LONGER USED

C. Pump Panel wiring

NOTICE: All wiring in this section should be done with 600V rated wire


1. Wire the 480VAC 3-Phase Power Supply attached to the DIN Rail
a) Using RED wire; connect Power Supply Terminals L1, L2, L3 to the top terminals of the Contactor ( i.e. Starter / Hammer ) L1, L2, L3 terminals
- Often this is easiest to do by wiring to a “Motor Saver” unit that is already wired to L1, L2, L3 if your panel has one
b) Using GREEN wire; connect Power Supply Ground (ꔍ) to a bolt or terminal connected to the panels back-plane

Illustration 2: All wires being yellow ( Use colors in instruction )


2. Wire the Solid State Relay attached to the DIN Rail
a) Using RED wire; connect Solid State Relay (15) → AUTO Terminal of the HAND-OFF-AUTO switch ( Typically the only unused terminal )
b) Using RED wire; connect Solid State Relay (16) →OPPOSITE side of the start button as the wire from the HAND-OFF-AUTO to the Start Button

3. Wire in the Pump-Panel Exit Plug
a) With the Plug end of the EXIT PLUG outside the box; insert the wires through a bottom hole in the Pumps Electrical Panel
b) Connect the
- Orange wire 24Vdc(+) → | of the Power Supply
- Brown wire 24Vdc(-) → | of the Power Supply
- Blue wire (A1)+ → | of the Solid State Relay
c) Verify that a BROWN wire already exists from 24Vdc(-) of the Power Supply →(A2)- of the Solid State Relay


4. Close the Electrical Panel – Panel Control installation is now complete
a) Wait until after installing the Pump-Controller before turning the breaker back on.
D. Pump-Controller
1. Plug the PUMP-CONTROLLER into the EXIT PLUG installed in the steps above.
2. Attach the PUMP-CONTROLLER box to the power pole using a wood screw at the desired height up the pole.
E. Testing
1. Turn the Electrical Panel Breaker ON.
2. Switch the Hand-Off-Auto switch to AUTO.
3. Using the HAND-REMOTE Device
a) Find the Menu-Item “Power” for the Pump-Controller Device just installed
b) Press ( ) to 'SET->' and then UP/DOWN to set to ON →

c) Press the square 'Enter' button – The pump should start running
d) While still on the “Power” Menu-Item; Press ( ) till 'SET->' and then UP/DOWN to set → to OFF
e) Press the square 'Enter' button – The pump should shut off

### 3. OPERATING INSTRUCTIONS

### 3.1 Introduction

The HAND-REMOTE display has a Top Row and a Bottom Row

✔ Top Row ( i.e. The Status Row – not changed directly )

◌ On the Left | - The Device ( Unit ) that is currently under control or being monitored
◌ On the Right | - The Alarms currently active ( Alarm 'ID'entifying letters )

✔ Bottom Row ( i.e. The Control Row – changes are made directly on this row )

◌ On the Left | - The current Menu-Item ( Up-Down Arrows Change Item )
◌ In the Middle | - The current Action/Function to be applied ( Right-Left Arrows Change )
- If it is (=) | - Function; Read Value for the current Menu-Item ( the “Main Menu” )
- If it is (SET ) → - Function; Set a New Value for the current Menu-Item
- If it is (<!) | - Function; Low Alarm value; “too-low” number value that will trigger alarm
- If it is (=!) | - Function; Low Alarm option; “is-equal-to” option that will trigger alarm
- If it is (>!) | - Function; High Alarm value; “too-high” number that will trigger alarm
- If it is (ǂ!) | - Function; High Alarm option; “not-equal-to” option that will trigger alarm
◌ On the Right | - The function Value ( of or for ) the Device ( Up-Down Arrows Change the SET
and/or ALARM VALUES )


( 3.1.1 OPERATING INSTRUCTIONS :: Introduction :: Display Table ) Page -14-

### 3.1.1 Display Table

✔ Maneuvering the display items can be represented as a table like the one shown below

◌ The “Location” Column is NOT part of the Display Menu; It shows where the item is wired to the Pump-Controller Hardware ( if applicable )
◌ Disabled items are Skipped when maneuvering through the display table
SUB-FUNCTIONS ( LEFT || RIGHT ) ← | → | Location
Device | MENU
ITEMS
(=)
Up/Down
Items
ENTER to
refresh

SET ( ) → Up/Down Changes ENTER to Apply

LOW ALARM (=!) (<!) Up/Down Changes ENTER Toggles On- Off | HI ALARM (ǂ!) (>!) Up/Down Changes ENTER Toggles On-Off | Wire to PIN ( NOT for Display )

Menu-Items ( UP || DO

WN ← ) →

Hand-Remote

Battery(B) | DISABLED | (<!) When less than

(>!) When greater
than

A1

Ditch Pump | Power(P) | (SET ) On → (SET ) Off → | (=!) Equals “On” (=!) Equals “Off” | (ǂ!) Not Equal “On” (ǂ!) Not Equal “Off”
Ditch Pump | Water (L) | DISABLED | (<!) When less than | (>!) When greater than
Ditch Pump | Pressure(R) | DISABLED | (<!) When less than | (>!) When greater than
Canal Pump | Power(P) | (SET ) On → (SET ) Off → | (=!) Equals “On” (=!) Equals “Off” | (ǂ!) Not Equal “On” (ǂ!) Not Equal “Off”
Canal Pump | Pressure(R) | DISABLED | (<!) When less than | (>!) When greater than

D7

V64(Trig=D4,E
cho=D5)
A3

D7

A3

Canal
Pump
Pressure(S) | DISABLED | (<!) When less than

(>!) When greater
than

A4

* Note: V64 is Virtual Pin #64; Virtual Pins are memory spaces inside the Pump-Controller and therefore the Pump-Controller firmware actually identifies the connecting pins. This is used when Pump-Controller processing is done before a legitimate value can be determined.

### 3.1.2 Alarms

✔ Alarms check read/monitored values against desired values ( Low / High boundaries ) and notifies the user ( buzzing ) if boundaries are violated

◌ Some menu items will have alarms while others will not – this is configured in the firmware and should be on a use-case scenario
◌ Anytime a button is pressed an active alarm ( buzzing ) will quite until “idle-monitoring” is started again ( No button press for 30-seconds )
◌ To permanently shut off the active alarm ( buzzing ) the alarm itself must be turned 'OFF'

✔ Alarms can be either turned ON or OFF

( 3.1.2 OPERATING INSTRUCTIONS :: Introduction :: Alarms ) Page -15-

◌ ON alarms are identified by the single character in the Top-Right of the Display
◌ Alarms are switched from ON OFF or OFF ON by → | →
- Press UP/DOWN until the Menu Item you'd like to turn an Alarm On/Off for - is selected
- Press RIGHT button to select which alarm to turn On/Off; Either the Low Alarm ( !=, !< ) or the High Alarm ( ! ǂ, !> )
- Press ENTER button to Toggle the Alarm On/Off ( An On-Alarm goes Off; An Off-Alarms goes On )

✔ To Set an alarm value
◌ Press UP/DOWN until the Menu Item you'd like to set an alarm boundary for is selected ◌ Press the RIGHT button as many times as it takes to see one of the following indicators in the Middle of the Bottom Row
- ( =! ) | - Sound an alarm if the value becomes EQUAL to the one indicated
- ( ǂ! ) | - Sound an alarm if the value does NOT-EQUAL equal the one indicated
- ( <! ) | - Sound an alarm if the value becomes LESS-THAN the one indicated
- ( >! ) | - Sound an alarm if the value becomes GREATER-THAN the one indicated
◌ Use the UP/DOWN buttons to select the comparison value or option
- For Numerical values; Holding the UP/DOWN button for more than 5 counts will increase or decrease the value by 10
◌ Press ENTER button to apply the selected comparison value ( Note; Applying a value will also Toggle the On/Off status of the Alarm )

✔ Notes
◌ When the Hand-Remote looses signal the alarms are shut-off automatically until signal is restored
◌ The Battery alarm will disable at any reading under 550. This prevents the battery from alarming while being powered by USB.

( 4. OPTIONAL ACCESSORIES :: OPTIONAL ACCESSORIES :: OPTIONAL ACCESSORIES ) Page -16-

### 4. OPTIONAL ACCESSORIES

Optional Accessories can be added to the Ag-irrigation Remote Control system to enhance monitoring and control abilities.

### 4.1 Hand-Remote

4.1.1 9V Rechargeable Batteries ( $18.90 )
It is highly recommended to purchase high output 300mAH or more rechargeable 9V Batteries; as the Hand-Remote will eat threw batteries pretty quickly.

At time of writing EBL 4x 600mAHh 9V Li-ion Rechargeable Batteries with Charger could be purchased for $18.90
http://www.ebay.com/itm/300974624904

NOTE: Even if a USB power is plugged in – If the power switch is turned ON it will still draw power from the battery. If you plug in USB for power be sure the power switch on the Hand-Remote unit is turned OFF.

### 4.2 Pump-Controller

### 4.2.1 Pressure

✔ Features
◌ Offers a way to remotely monitor the water pressure ◌ Default programming on pin A3
A. Materials ($9.59)


5V 0-1.2 MPa Pressure Transducer Sensor Oil Fuel Diesel Gas Water Air Sensor Banggood.com (http://www.banggood.com/Pressure-Transducer-Sensor-Oil-Fuel-Diesel-Gas-Water-Air-Sensor-p-1007341.html) ( $9.59/EA )

required to reach from the pipe to the Pump-Controller

B. Installation

( 4.2.1 OPTIONAL ACCESSORIES :: Pump-Controller :: Pressure ) Page -17-

1. Remove the current Pressure Gauge from its location
2. Screw in the Pressure Transducer ( Typically does fit the same hole size and threads as the pressure gauge )
3. Wire up the Transducer as follows
a) Transducer RED wire ( +5V ) Cat5e ORANGE →
b) Transducer BLACK wire ( GND ) Cat5e BROWN →
c) Transducer YELLOW wire ( SIGNAL ) Cat5e BLUE →
4. Wire the other end of the Cat5e Wire into the Pump-Controller
a) Cat5e ORANGE 5VDC →
b) Cat5e BROWN GND →
c) Cat5e BLUE A3 →


C. Firmware Adjustments

See #5.1.Adding Expansions|outline
To activate the Pressure Sensor on the Hand-Remote Unit

### 4.2.2 Water Level

✔ Features
◌ Offers a way to remotely monitor water-level in a ditch
◌ Default programming on pins D4 (TRIG) and D5 (ECHO) – On Pump-Controllers Firmware
A. Materials ( $10.77/ea )


( 4.2.2 OPTIONAL ACCESSORIES :: Pump-Controller :: Water Level ) Page -18-

(1) DC 5V Waterproof Ultrasonic Module Distance Measuring Transducer Sensor banggood.com (http://www.banggood.com/DC-5V-Waterproof-Ultrasonic-Module-Distance-Measuring-Transducer-Sensor-p-1094462.html) ( $ 10.77/EA )
(1) 4-PIN Female Dupont Header to connect to Circuit Board Pins ( See Dupont Headers in BOM )
B. 3D-Prints ( $1.30 )

✔ Print the Following Models on a 3D-Printer
◌ Files Located at
https://github.com/tgit23/AgIrrigationRemoteControl/tree/master/Accessories/Sonic%20Water%20Level%20Meter/3D-Prints-STL (https://github.com/tgit23/AgIrrigationRemoteControl/tree/master/Accessories/Sonic%20Water%20Level%20Meter/3D-Prints-STL)
◌ Total Filament = 43.7 cm3 @ $0.03/cm3 ~ $1.30
SonicCircuitBoardCase.stl ( 14.3 cm3 ) | SonicCableCover.stl ( 2.5 cm3 ) | SonicCircuitBoardCover.stl ( 6.7 cm
SonicHeadCase.stl ( 17.6 cm3 ) | SonicHeadCover.stl ( 2.6 cm3 )
C. Firmware Adjustments

See 4.1.Adding Expansions
To activate the Ultrasonic Distance Water Level Meter on the Hand-Remote Unit

( 4.2.3 OPTIONAL ACCESSORIES :: Pump-Controller :: Auxiliary Contact ( $43.75 ) ) Page -19-

### 4.2.3 Auxiliary Contact ( $43.75 )


✔ Auxiliary contact, side mounted, 1 N.O. Contact ( NOTE: This must match/fit the pump panels Contactor Unit )
◌ https://www.automationdirect.com/adc/Shopping/Catalog/Motor_Controls/Eaton_Cutler-Hammer_Contactors_-z-_Starters_-z-_Overloads/Auxiliary_Contacts/C320KGS1 (https://www.automationdirect.com/adc/Shopping/Catalog/Motor_Controls/Eaton_Cutler-Hammer_Contactors_-z-_Starters_-z-_Overloads/Auxiliary_Contacts/C320KGS1) -$43.75/ea

✔ Notes
◌ Auxiliary Contactor must be purchased according to the contactor they will FIT on.
- The above suggested purchase will ONLY work with the NEMA-2 Model # AN16GNO Series B1 Contactor
◌ The Auxiliary Contactor typically already used by the Start-lock CANNOT be used for this purpose as it has 480V wires already attached to it.
◌ Often a used aux contactor can be found much cheaper on ebay

✔ Benefits
◌ Offers a way to monitor the actual (i.e. directly) the pump power status

### 5. TROUBLESHOOTING

✔ Support
◌ You can email me at tgit28@gmail.com with any questions, comments and or requests. I'm glad to help in any way I can.

✔ Hand-Remote Problems

◌ The Display is or started to show garbage
- Typically this is a symptom of a low battery ( Replace the 9V Battery and see if that fixes the problem )

◌ The Menu-Items all show 'ERR' ( Meaning it cannot communicate with the Pump-Controller )

- 1) Unplug the Pump-Controller Box at the Pump-Panel EXIT PLUG
- 2) Measure voltage across the two center pins; It should read approximately 24Vdc. If it doesn't --
- Double check that the main breaker is ON
- If the pins still do not read voltage; double check the installation steps ( Make sure to turn OFF the main breaker before opening the panel )
- 3) If 24Vdc is measured at the Exit Plug ---
- Remove the PUMP-CONTROLLER cover

( 5. TROUBLESHOOTING :: TROUBLESHOOTING :: TROUBLESHOOTING ) Page -20-

- Measure voltage from the screw terminals labeled 5Vdc and GND; It should read approximately 5Vdc. If it doesn't --
- Check that the DC power plug is plugged into the Arduino ( See BOM to determine which board is the Arduino )
- Check that board lights are lit and one should be blinking
- 4) If all the above is Okay
- There may be a more serious problem like a solder joint has come UN-done or system configuration was lost.
- You can try and re-configure the Xbee and Upload Firmware again; but the unit is deemed broken and should be returned for a replacement

✔ Pump-Controller Problems

◌ The Pump doesn't turn ON although the Hand-Remote displays that Power is ON

- 1) Be sure the Hand-Off-Auto Selector switch is set to Auto
- 2) Double check the installation steps ( Make sure to turn OFF the main breaker before opening the panel )
- Note: If the Solid State Relay was wired on the wrong side of the Start Button; this will cause a short when the Power was Set ON on the Hand-Remote and the Solid State → Relay may be fried and will need to be replaced.

### 6. FCC Compliance

✔ An FCC compliance label showing the following should be attached to each device that contains the Xbee Module

Contains FCC ID: OUR-XBEEPRO
The enclosed device complies with Part 15 of the FCC Rules. Operation is subject to the following two conditions: (i. ) this device may not cause harmful interference and (ii. ) this device must accept any interference received, including interference that may cause undesired operation.

✔ The User Manual should contain the following

CAUTION! To satisfy FCC RF exposure requirements for mobile transmitting devices, a separation distance of 20 cm or more should be maintained between the antenna of this device and persons during device operation. To ensure compliance, operations at closer than this distance is not recommended. The antenna used for this transmitter must not be co-located in conjunction with any other antenna or transmitter.

✔ See
https://www.digi.com/resources/documentation/Digidocs/90000991/reference/r_certs_xb_usa.htm for more information

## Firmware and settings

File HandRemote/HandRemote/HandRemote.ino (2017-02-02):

/*********************************************************************************//**
 * @brief  Arduino Sketch firmware to be uploaded onto the Ag-Irrigation Hand-Remote 
 * @see https://github.com/tgit23/AgIrrigationRemoteControl
 * @todo
 *  - Need a good way to monitor multiple pumps
 * @authors 
 *    tgit23        01/2017       Original
*************************************************************************************/
#include <LiquidCrystal.h>
#include <EEPROM.h>
#include <PeerIOSerialControl.h> //See https://github.com/tgit23/PeerIOSerialControl
#define DEBUG 1
#if DEBUG>0
  #define DBL(x) Serial.println x
  #define DB(x) Serial.print x
  #define DBC Serial.print(", ")
#else
  #define DBL(x)
  #define DB(x)
  #define DBC  
#endif

//---[ IO-PIN SETTINGS ]--------------------------------------------------------------
#define SBUZZ 2                 // Signal-Pin on Buzzer
#define SS_TX_PIN 11            // Pin 2 is used by Buzzer
#define SS_RX_PIN 12            // Pin 10 is input backlight LCD; pin 8,9 are LCD
#define BATT_PIN 1
LiquidCrystal lcd(8, 9, 4, 5, 6, 7);          // select the pins used on the LCD panel

//---[ PROGRAM BEHAVIOR SETTINGS ]----------------------------------------------------
#define WAIT_REPLY_MS         1000      // How long to wait for a XBee reply
#define START_STATUS_ITERATE  15000     // Start iterating statuses after idle (ms)
#define ITERATE_EVERY         3000      // Iterate Status every (ms)

//---[ STATIC SETTINGS ]---------------------------------------------------------------
// Val[] Indexes
#define MAIN 0                // The current-read value of the Menu Item
#define SET 1                 // Value used to SET a MAIN-Value
#define LOALARM 2             // Value used for a Low Alarm on MAIN-Value
#define HIALARM 3             // Value used for a High Alarm on MAIN-Value
#define VALITEMS 4            // Total number of Value's per Menu Item

// Setup a Software Serial for XBEE (Allows Debug)
#include <SoftwareSerial.h>
SoftwareSerial IOSerial(SS_RX_PIN,SS_TX_PIN);   // ( rxPin, txPin )
PeerIOSerialControl XBee(1,IOSerial,Serial);    // ArduinoID, IOSerial, DebugSerial

enum Button { UP, DOWN, RIGHT, LEFT, SELECT, NONE };
enum eValueLocation { 
  PROG, LOCALPIN_DIGITAL, LOCALPIN_ANALOG, REMOTEPIN_DIGITAL, REMOTEPIN_ANALOG, EPROM };
unsigned long last_bpress = 0;                // Track last button press time
unsigned long last_change = 0;                // Track last status iteration time
int idx = 0;
int ValIdx = MAIN;

//---[ MENU STRUCTURE ]----------------------------------------------------------------
#define MENUITEMS 5                           // # of Menu Items ( 1 + index )
#define MAXOPTIONS 2                          // Maximum # of Options allowed
#define PUMPIDX 0                             // Menu-idx of Select Pump Location
#define PUMPADDR 1020                         // EEPROM address to store Selected Pump
#define STARTIDX 1                            // First Menu item displayed after reset

/*********************************************************************************//**
 * @brief  User-defined data structure for Menu Items that use a Pick-Option method
*************************************************************************************/
struct uItemOption {
  char *Text;
  int Value = LOW;
  uint8_t PumpID = 0;                         // Special place for Target AduinoID
};

/*********************************************************************************//**
 * @brief  User-defined data structure for MAIN, SET, LOALARM, HIALARM Values.
*************************************************************************************/
struct uValues {
  int Value = -1;
  int ToneHz = 1000;
  char ID = NULL;         // A set ID activates the alarm setting in the menu
  bool Active = false;    // [MAIN]Active=Valid, [SET]Active=Settable, ALARM=Is ON
};

/*********************************************************************************//**
 * @brief  User-defined data structure for every Menu Item ( Value ) on the Unit
*************************************************************************************/
struct MenuItems {
  char *Text;
  uValues Val[VALITEMS];
  eValueLocation ValueLocation = PROG;      // PROG = Internally in Program
  byte Pin = 0;                             // Arduino Pin#, Analog/Digital Set below
  uItemOption Option[MAXOPTIONS];
  byte LastOption = 0;                      // If entry doesn't have options its numeric
  bool Poll=true;
} Menu[MENUITEMS];

/*********************************************************************************//**
 * @brief  Record Menu Item Values in EEPROM non-volitale memory.
 * @remarks
 * - Arduino UNO offers 1024-bytes or (146)7-Byte Menu Item Storage
 * - Using 980-bytes or (140)7-Byte Values allowing Pump Select over byte 1000-Address
 * - Limits (4)Pumps with (35)7-Byte Values = (245)Bytes per Pump or (980)Bytes Total
 * - This function is also called on all Menu Items to set Alarm values into EEPROM.
 *  @code
 *    exmaple code
 *  @endcode
*************************************************************************************/
void EEPROMSet(int i = -1) {
  if ( i == -1 ) i = idx;DBL(("EEPROMSet()"));
  int iPumpOffset = Menu[PUMPIDX].Val[MAIN].Value * 245;
  
  if ( i == PUMPIDX ) {
    EEPROM.update(PUMPADDR,(char)Menu[i].Val[MAIN].Value);    // Write
    EEPROM.update(PUMPADDR+1,0x22);                           // Validate in EEPROM
    Menu[i].Val[MAIN].Active = true;
  
  } else {
    // Store Value in EEPROM
    if ( Menu[i].ValueLocation == EPROM ) {
      byte valLowByte = ((Menu[i].Val[MAIN].Value >> 0) & 0xFF);
      byte valHighByte = ((Menu[i].Val[MAIN].Value >> 8) & 0xFF);
      
      EEPROM.update( (i*7+0)+iPumpOffset, valLowByte);
      DB(("EEPROM.update( "));DB(((i*7+0)+iPumpOffset));
      DBC;DB((valLowByte, HEX));DBL((")"));
      
      EEPROM.update( (i*7+1)+iPumpOffset, valHighByte);
      DB(("EEPROM.update( "));DB(((i*7+1)+iPumpOffset));
      DBC;DB((valHighByte, HEX));DBL((")"));
    }
    
    // Store Alarm Values in EEPROM
    byte loAlarmLoByte = ((Menu[i].Val[LOALARM].Value >> 0) & 0xFF);
    byte loAlarmHiByte = ((Menu[i].Val[LOALARM].Value >> 8) & 0xFF);
    byte hiAlarmLoByte = ((Menu[i].Val[HIALARM].Value >> 0) & 0xFF);
    byte hiAlarmHiByte = ((Menu[i].Val[HIALARM].Value >> 8) & 0xFF);
    byte AlarmSet = 0x22;   // 2=OFF, A=ON
    if ( Menu[i].Val[LOALARM].Active ) bitSet(AlarmSet,3);
    if ( Menu[i].Val[HIALARM].Active ) bitSet(AlarmSet,7);
    
    EEPROM.update( (i*7+2)+iPumpOffset, loAlarmLoByte);
    DB(("EEPROM.update( "));DB(((i*7+2)+iPumpOffset));
    DBC;DB((loAlarmLoByte, HEX));DBL((")"));
    
    EEPROM.update( (i*7+3)+iPumpOffset, loAlarmHiByte);
    DB(("EEPROM.update( "));DB(((i*7+3)+iPumpOffset));
    DBC;DB((loAlarmHiByte, HEX));DBL((")"));
    
    EEPROM.update( (i*7+4)+iPumpOffset, hiAlarmLoByte);
    DB(("EEPROM.update( "));DB(((i*7+4)+iPumpOffset));
    DBC;DB((hiAlarmLoByte, HEX));DBL((")"));
    
    EEPROM.update( (i*7+5)+iPumpOffset, hiAlarmHiByte);
    DB(("EEPROM.update( "));DB(((i*7+5)+iPumpOffset));
    DBC;DB((hiAlarmHiByte, HEX));DBL((")"));
    
    EEPROM.update( (i*7+6)+iPumpOffset, AlarmSet);
    DB(("EEPROM.update( "));DB(((i*7+6)+iPumpOffset));
    DBC;DB((AlarmSet, HEX));DBL((")"));
  }
}

/*********************************************************************************//**
 * @brief  Read Menu Item Values from Arduino EEPROM non-volitale memory.
 * @see    EEPROMSet for Addressing notation
 * @code
 *   exmaple code
 * @endcode
*************************************************************************************/
void EEPROMGet(int i = -1) {
  byte StatusByte = 0;
  if ( i == -1 ) i = idx;
  
  if ( i == PUMPIDX ) {
    Menu[i].Val[MAIN].Value = (int)EEPROM.read(PUMPADDR);
    if (EEPROM.read(PUMPADDR+1) == 0x22) Menu[i].Val[MAIN].Active = true;
  } else {
    // Get Values from EEPROM
    int iPumpOffset = Menu[PUMPIDX].Val[MAIN].Value * 245;
    if ( Menu[i].ValueLocation == EPROM ) {
      byte valLowByte = EEPROM.read( ((i*7+0)+iPumpOffset) );
      byte valHighByte = EEPROM.read( ((i*7+1)+iPumpOffset) );
      Menu[i].Val[MAIN].Value = (int)((valLowByte << 0) & 0xFF) + ((valHighByte << 8) & 0xFF00);
    }

    // Get Alarm Values from EEPROM
    byte loAlarmLoByte = EEPROM.read( ((i*7+2)+iPumpOffset) );
    byte loAlarmHiByte = EEPROM.read( ((i*7+3)+iPumpOffset) );
    byte hiAlarmLoByte = EEPROM.read( ((i*7+4)+iPumpOffset) );
    byte hiAlarmHiByte = EEPROM.read( ((i*7+5)+iPumpOffset) );
    byte AlarmSet = EEPROM.read( ((i*7+6)+iPumpOffset) );
    
    Menu[i].Val[LOALARM].Value = (int)((loAlarmLoByte << 0) & 0xFF) + ((loAlarmHiByte << 8) & 0xFF00);
    Menu[i].Val[HIALARM].Value = (int)((hiAlarmLoByte << 0) & 0xFF) + ((hiAlarmHiByte << 8) & 0xFF00);
    Menu[i].Val[LOALARM].Active = bitRead(AlarmSet,3);
    Menu[i].Val[HIALARM].Active = bitRead(AlarmSet,7);

    // EPROM Values are 'Active' if the AlarmSet Bit Check passes ( Value was set/not garbage )
    if ( Menu[i].ValueLocation == EPROM ) {
      if ( (AlarmSet & 0x77) == 0x22 ) Menu[i].Val[MAIN].Active = true;
    }
  }

}

/*********************************************************************************//**
 * @brief  Preforms all needed changes to the system when changing a Selected Pump.
 * @code
 *   exmaple code
 * @endcode
*************************************************************************************/
void SetPump(int PumpID) {
  
  if ( PumpID != XBee.TargetArduinoID() ) {
    for (int i=0;i<MENUITEMS;i++) {
      if ( i != PUMPIDX ) {
        Menu[i].Val[MAIN].Active = false;     // De-Activate previouse Read's
        EEPROMGet(i);                         // Load Alarm Values
      }
    }
    XBee.TargetArduinoID(PumpID);
  }
  
}

/*********************************************************************************//**
 * @brief  Obtain menu values and compare them against their alarm values
 * @remarks
 *  - Battery read 458 when running off USB and 856 when running from 9VDC Battery.
 * @code
 *   exmaple code
 * @endcode
*************************************************************************************/
void GetItem(int i = -1) {
  if ( i == -1 ) i = idx;DBL(("GetItem()"));

  // Make sure we have a valid Pump Selected
  if ( i != PUMPIDX && !Menu[PUMPIDX].Val[MAIN].Active ) return;

  if ( Menu[i].ValueLocation == EPROM ) {
      EEPROMGet();          // Read Value from EEPROM
  } else {
    if ( Menu[i].ValueLocation == LOCALPIN_DIGITAL ) {
      Menu[i].Val[MAIN].Value = digitalRead(Menu[i].Pin);
    } else if ( Menu[i].ValueLocation == LOCALPIN_ANALOG ) {
      Menu[i].Val[MAIN].Value = analogRead(Menu[i].Pin);
    } else if ( Menu[i].ValueLocation == REMOTEPIN_DIGITAL ) {
      Menu[i].Val[MAIN].Value = XBee.digitalReadB(Menu[i].Pin);
    } else if ( Menu[i].ValueLocation == REMOTEPIN_ANALOG ) {
      Menu[i].Val[MAIN].Value = XBee.analogReadB(Menu[i].Pin);
    }
    if ( Menu[i].Val[MAIN].Value != -1 ) Menu[i].Val[MAIN].Active = true;
  }

  // Check this Value for an Active Alarm
  if ( Menu[i].Val[MAIN].Active ) {
    if ( Menu[i].Val[LOALARM].Active && Menu[i].Val[LOALARM].ID != NULL ) {
      if ( Menu[i].LastOption > 0 ) {
        if ( Menu[i].Val[MAIN].Value == Menu[i].Val[LOALARM].Value ) tone(SBUZZ,Menu[i].Val[LOALARM].ToneHz);
      } else {
        if ( Menu[i].Val[MAIN].Value < Menu[i].Val[LOALARM].Value ) tone(SBUZZ, Menu[i].Val[LOALARM].ToneHz);
      }
    }
    if ( Menu[i].Val[HIALARM].Active && Menu[i].Val[HIALARM].ID != NULL ) {
      if ( Menu[i].Val[MAIN].Value > Menu[i].Val[HIALARM].Value ) tone(SBUZZ, Menu[i].Val[HIALARM].ToneHz);
    }
  }
}

/*********************************************************************************//**
 * @brief  Preform value setting and recording when the 'Select' button is pressed.
 * @code
 *   exmaple code
 * @endcode
*************************************************************************************/
void SetItem(int i = -1) {
  if ( i == -1 ) i = idx;int iSetValue = 0;DBL(("SetItem()"));
  if ( i != PUMPIDX && !Menu[PUMPIDX].Val[MAIN].Active ) return;  // No control till a pump is selected

  // ALARM - If viewing an Alarm Value - Select will Toggle the Alarm ON/OFF
  if ( ValIdx == LOALARM || ValIdx == HIALARM ) {
    Menu[i].Val[ValIdx].Active = !Menu[i].Val[ValIdx].Active;
    if ( Menu[i].ValueLocation != EPROM ) EEPROMSet();

  // MAIN - If viewing a 'MAIN' Value; Select will Refresh the Value
  } else if ( ValIdx == MAIN ) {
    GetItem();

  // SET - If viewing a 'SET' Value; Select will Set the Value
  } else if ( ValIdx == SET ) {

    if ( ValIdx != SET ) return;
  
    // Obtain the Set Value
    iSetValue = Menu[i].Val[SET].Value;
    if ( Menu[i].LastOption > 0 ) {
      if (Menu[i].Val[SET].Value < 0 || Menu[i].Val[SET].Value > MAXOPTIONS) return;
      iSetValue = Menu[i].Option[Menu[i].Val[SET].Value].Value;
    }
    Menu[i].Val[MAIN].Active = false; // Remove the last Read Value; its changing

    switch ( Menu[i].ValueLocation ) {
      case EPROM:
        Menu[i].Val[MAIN].Value = Menu[i].Val[SET].Value;   // Set the Value
        EEPROMSet();                                        // Write the Value to EEPROM
        Menu[i].Val[MAIN].Active = true;                    // Validate
        if ( i == PUMPIDX ) SetPump( Menu[i].Option[ Menu[i].Val[MAIN].Value ].PumpID );
        break;

      case LOCALPIN_DIGITAL:
        Menu[i].Val[MAIN].Active = true;
        digitalWrite(Menu[i].Pin, iSetValue);
        break;

      case LOCALPIN_ANALOG:
        analogWrite(Menu[i].Pin, iSetValue);
        break;

      case REMOTEPIN_DIGITAL:
        XBee.digitalWriteNB(Menu[i].Pin, iSetValue);
        break;

      case REMOTEPIN_ANALOG:
        XBee.analogWriteNB(Menu[i].Pin, iSetValue);
        break;
    }
  }
}

/*********************************************************************************//**
 * @brief  Setup the LCD menu
 * @remarks
 * - Allows a single spot customization to users configuration
 * @code
 *   exmaple code
 * @endcode
*************************************************************************************/
void SetupMenu() {

  // Be sure to change 'MENUITEMS' when adding/deleting items
  Menu[PUMPIDX].Text = "Pump";
  Menu[PUMPIDX].ValueLocation = EPROM;
  Menu[PUMPIDX].Option[0].Text = "Canal";
  Menu[PUMPIDX].Option[0].PumpID = 10;           // Target ArduinoID
  Menu[PUMPIDX].Option[1].Text = "Ditch";
  Menu[PUMPIDX].Option[1].PumpID = 11;           // Target ArduinoID
  Menu[PUMPIDX].LastOption = 1;
  Menu[PUMPIDX].Poll=false;                     // Poll for Updates
  Menu[PUMPIDX].Val[SET].Active = true;
  
  Menu[1].Text = "Power";
  Menu[1].ValueLocation = REMOTEPIN_DIGITAL; 
  Menu[1].Option[0].Text = "Off";   
  Menu[1].Option[0].Value = LOW;  
  Menu[1].Option[1].Text = "On";
  Menu[1].Option[1].Value = HIGH;
  Menu[1].LastOption = 1;
  Menu[1].Pin = 7;
  Menu[1].Val[SET].Active = true;             // Allows Value to be 'SET'
  Menu[1].Val[LOALARM].ID = 'p';

  Menu[2].Text = "Water L.";
  Menu[2].ValueLocation = REMOTEPIN_ANALOG; 
  Menu[2].Pin = 64;
  Menu[2].Val[LOALARM].ID = 'l';
  Menu[2].Val[HIALARM].ID = 'L';
  
  Menu[3].Text = "Battery";
  Menu[3].ValueLocation = LOCALPIN_ANALOG;
  Menu[3].Pin = BATT_PIN; // Analog A2
  Menu[3].Val[LOALARM].ID = 'b';
  
  Menu[4].Text = "Pressure";
  Menu[4].ValueLocation = REMOTEPIN_ANALOG;
  Menu[4].Pin = 0;
  Menu[4].Val[LOALARM].ID='r';
  Menu[4].Val[HIALARM].ID='R';
    
  // Read all values at start-up
  GetItem(PUMPIDX);
  SetPump( Menu[PUMPIDX].Option[ Menu[PUMPIDX].Val[MAIN].Value ].PumpID );
  idx = STARTIDX;
}

/*********************************************************************************//**
 * @brief  Properly display a Menu Item on the LCD screen
 * @code
 *   exmaple code
 * @endcode
*************************************************************************************/
void LCD_display() {
  
  // Top Row (Status)
  lcd.clear();lcd.setCursor(0,0);
  if(Menu[PUMPIDX].Val[MAIN].Active) { 
    lcd.print(Menu[PUMPIDX].Option[Menu[PUMPIDX].Val[MAIN].Value].Text);
    lcd.setCursor(strlen(Menu[PUMPIDX].Option[Menu[PUMPIDX].Val[MAIN].Value].Text)+1,0);lcd.print("Pump");
  } else {
    lcd.print("ERR Pump");
  }
  
  // Alarm Statuses
  int pos = 15;
  for (int i=0;i<MENUITEMS;i++) {
    if ( Menu[i].Val[LOALARM].Active && Menu[i].Val[LOALARM].ID != NULL ) {
      lcd.setCursor(pos,0);lcd.print(Menu[i].Val[LOALARM].ID);pos--;
    }
    if ( Menu[i].Val[HIALARM].Active && Menu[i].Val[HIALARM].ID != NULL ) {
      lcd.setCursor(pos,0);lcd.print(Menu[i].Val[HIALARM].ID);pos--;
    }
  }
  
  // Menu Item Text on Bottom Row
  lcd.setCursor(0,1);lcd.print(Menu[idx].Text);
  lcd.setCursor(strlen(Menu[idx].Text),1);
  
  if ( ValIdx == MAIN ) {
    lcd.print(" =");
    lcd.setCursor(strlen(Menu[idx].Text)+2,1);
  } else if ( ValIdx == SET ) {
    lcd.print(" Set");
    lcd.print((char)126); //Character '->'
    lcd.setCursor(strlen(Menu[idx].Text)+5,1);
  } else {
    if ( Menu[idx].LastOption > 0 ) {
      lcd.print(" !=");
    } else {
      if ( ValIdx == LOALARM) lcd.print(" !<");
      if ( ValIdx == HIALARM) lcd.print(" !>");
    }
    lcd.setCursor(strlen(Menu[idx].Text)+3,1);
  }
  
  // Value
  if ( ValIdx == MAIN && !Menu[idx].Val[MAIN].Active ) {
    lcd.print("ERR");
  } else {
    if ( Menu[idx].LastOption > 0 ) {
      int OptionIdx = Menu[idx].Val[ValIdx].Value;
      if( OptionIdx < 0 || OptionIdx > Menu[idx].LastOption ) {
        lcd.print("ERR-");lcd.print(OptionIdx);
      } else {
        lcd.print(Menu[idx].Option[OptionIdx].Text); 
      }
    } else {
        lcd.print(Menu[idx].Val[ValIdx].Value);
    }
  }
  delay(200);
}


/*********************************************************************************//**
 * @brief  Arduino Sketch Setup routine - Initialize the environment.
 * @remarks
 * - pin#10 INPUT Backlit shorting see http://forum.arduino.cc/index.php?topic=96747.0
 * @code
 *   exmaple code
 * @endcode
*************************************************************************************/
void setup(){
    pinMode(10,INPUT);            // Fix for Q1-LCD Backlit shorting issue
    pinMode(SBUZZ,OUTPUT);
    pinMode(SS_RX_PIN, INPUT);
    pinMode(SS_TX_PIN, OUTPUT);
    
    IOSerial.begin(9600);
    Serial.begin(9600);           // Start UART Communications with the XBee->Module
    lcd.begin(16, 2);             // Start the LCD library
    SetupMenu();
    XBee.Timeout(WAIT_REPLY_MS);  // Set the Timeout
    LCD_display();                // Display the main menu
}

/*********************************************************************************//**
 * @brief  Arduino Sketch Loop() routine
 * @remarks
 * - This function is called automatically over-and-over by Arduino
 * - Handles incoming XBee communications
 * - Handles button presses and LCD response updates
 * - Handles Menu iteratation during idle.
*************************************************************************************/
void loop(){

  // Check for a button press
  Button bpress = NONE;
  int adc_key_in = analogRead(0);
  if (adc_key_in > 1000) { bpress = NONE; }
  else if (adc_key_in < 50) { bpress = RIGHT; }
  else if (adc_key_in < 195) { bpress = UP; }
  else if (adc_key_in < 380) { bpress = DOWN; }
  else if (adc_key_in < 555) { bpress = LEFT; }
  else if (adc_key_in < 790) { bpress = SELECT; }

  // Check for incoming communications
  XBee.Available();

  // Preform duties
  if(bpress == NONE) {
    if ( millis() - last_bpress > START_STATUS_ITERATE && 
         millis() - last_change > ITERATE_EVERY ) {
          
          ValIdx = MAIN;
          int i = idx;                  // Mark current idx
          do {
            i++;if(i>MENUITEMS-1) i=0;  // reset idx to beginning
            if(i == idx) break;         // break if made a full rotation
          } while (!Menu[i].Poll);      // stop if item is Poll
          idx=i;                        // set new 'idx' to next with a Poll
          GetItem();
          last_change=millis();
          LCD_display();
    }
  } else { last_bpress = millis(); }
  
  if(bpress !=NONE) {
    noTone(SBUZZ);

      if (bpress == SELECT) {
        SetItem();
      
      } else if (bpress == UP) {
        ValIdx = MAIN;
        idx--;if(idx<0) idx=MENUITEMS-1;
        if ( !Menu[idx].Val[MAIN].Active ) GetItem();
        
      } else if (bpress == DOWN) {
        ValIdx++;
        if ( ValIdx == SET && !Menu[idx].Val[SET].Active ) ValIdx++;      // Skip SET if not Active
        if ( ValIdx == LOALARM && Menu[idx].Val[LOALARM].ID == NULL ) ValIdx++;
        if ( ValIdx == HIALARM && Menu[idx].Val[HIALARM].ID == NULL ) ValIdx++;    // Skip HIALARM if Option
        if ( ValIdx > VALITEMS-1 ) {
          ValIdx = 0;
          idx++;if(idx>MENUITEMS-1) idx=0;
        }
        if ( ValIdx == MAIN && !Menu[idx].Val[MAIN].Active ) GetItem();
      }    

      // Change the Value
      if ( ValIdx != MAIN ) {
        if (bpress == RIGHT) {
          Menu[idx].Val[ValIdx].Value++;
          if ( Menu[idx].LastOption>0 && Menu[idx].Val[ValIdx].Value > Menu[idx].LastOption) Menu[idx].Val[ValIdx].Value = 0;
        
        } else if(bpress == LEFT) {
          if ( Menu[idx].Val[ValIdx].Value > 0 ) Menu[idx].Val[ValIdx].Value--;
          if ( Menu[idx].LastOption>0 && Menu[idx].Val[ValIdx].Value > Menu[idx].LastOption) Menu[idx].Val[ValIdx].Value = Menu[idx].LastOption;
        }
      }

    // Update Display
    LCD_display();
  }
}

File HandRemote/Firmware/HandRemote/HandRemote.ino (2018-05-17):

/******************************************************************************************************************//**
 * @brief  Arduino Sketch firmware to be uploaded onto the AgIrrigationRemoteControl Hand-Remote Device.
 * @see https://github.com/tgit23/AgIrrigationRemoteControl
 * @remarks Version 2017.06.17
 * @todo
 *  - Implement Firmata for Base/Desktop operation
 * @authors 
 *    tgit23        01/2017       Original
 *    tgit23        07/2017       Implemented keypad button interrupts and Non-Blocking functionality
**********************************************************************************************************************/
#include <LiquidCrystal.h>
#include <EEPROM.h>
#include <PeerIOSerialControl.h>        //See https://github.com/tgit23/PeerIOSerialControl
#include <SSoftwareSerial.h>            //See 

//=====================================================================================================================
//------------------------------ SIMPLE USER CONFIGURATION SETTINGS ---------------------------------------------------
//=====================================================================================================================
#define BUILD_VERSION                     20170706  // Release Version used to Build the Unit ( without the dots )
#define TRANSCEIVER_ID                    1         // Unique numeric (ID)entity for this Unit(1-15)
#define XBEECONFIG                        0         // Configure the XBEE using XCTU Digi Software by setting this to 1
#define ULTRASONIC_WATER_LEVEL_INSTALLED  0         // 0 = NO, 1 = YES ( Wire TRIG -> D4, ECHO -> D5 )
#define WATER_PRESSURE_INSTALLED          0         // 0 = NO, 1 = YES ( Wire SENSE -> A3 )

//^^^[ END - SIMPLE USER CONFIGURATION SETTINGS ]^^^^^^^^^^^^^^^^^^^^^^^^^^^^^^^^^^^^^^^^^^^^^^^^^^^^^^^^^^^^^^^^^^^^^^
//---------------------------------------------------------------------------------------------------------------------

//---[ PROGRAM BEHAVIOR ]----------------------------------------------------------------------------------------------
#define WAIT_REPLY_MS         3000      // How long to wait for an XBee reply
#define START_STATUS_ITERATE  30000     // Start iterating Menu-Items after idle for (ms)
#define ITERATE_EVERY         5000      // Iterate Menu-Items every (ms); when idle
#if XBEECONFIG>0
#define NONBLOCKING           0         // Digi-Xbee-XCTU configuration software has problems with active interupts
#else
#define NONBLOCKING           1         // Blocking mode (0) stalls screen till item is gotten, (1) releases screen
#endif
#define DEBUG                 0         // Set this to 1 for Serial DEBUGGING messages ( Firmware development use only )
#if DEBUG>0                             // Activate Debug Messages
  #define DBL(x) Serial.println x
  #define DB(x) Serial.print x
  #define DBC Serial.print(", ")
#else                                   // ELSE - Clear Debug Messages
  #define DBL(x)
  #define DB(x)
  #define DBC  
#endif

//---[ HAND-REMOTE PIN SETTINGS ]--------------------------------------------------------------------------------------
LiquidCrystal lcd(8, 9, 4, 5, 6, 7);    // Pins used by the LCD Keypad Shield
#if BUILD_VERSION>20170524
  #define SS_TX_PIN 2                     // TX -> XBEE-DIN ( Closest to UNO )
  #define SS_RX_PIN 3                     // RX -> XBEE-DOUT ( Farthest from UNO )
  #define SBUZZ 12                        // Buzzer Signal Pin (S)
  #define PBUZZ 13                        // Buzzer Power Pin (+)
#else                                   // vvvvvvvv [ Build Release 2017.05.24 Pins ] vvvvvvvvvvvvvv
  #define SS_TX_PIN 11                    // TX -> XBEE-DIN ( Closest to UNO )
  #define SS_RX_PIN 12                    // RX -> XBEE-DOUT ( Farthest from UNO )
  #define SBUZZ 2                         // Buzzer Signal Pin (S)
#endif                                  // ^^^^^^^^^^^^^^^^^^^^^^^^^^^^^^^^^^^^^^^^^^^^^^^^^^^^^^^^^
#define BATT_R1_VINTOA1   1500          // Integer Value of BATTVOLT Resistor VIN -> A1 in KOhms
#define BATT_R2_A1TOGND   510           // Integer Value of BATTVOLT Resistor A1 -> GND in KOhms

//---[ PROGRAM CONSTANTS ]---------------------------------------------------------------------------------------------
enum Button       { UP, DOWN, RIGHT, LEFT, SELECT, NONE };
enum eValModifier { RAW, PRESSURE, BATTVOLTS };
#define NOPIN     0xFF                // 255 (unit8_t) = 'NOPIN'
#define MAIN      0                   // Menu[#].Sub[0-MAIN] for currently-read value of the Menu Item
#define VALID     true                // Is Menu[#].Sub[MAIN].State a 'VALID' (read) value?
#define SET       1                   // Menu[#].Sub[1-SET] for SET values to await being applied to the MAIN-Value
#define SETTABLE  true                // Does Menu[#].Sub[SET].State allow 'SETTABLE' values by the user
#define LOALARM   2                   // Menu[#].Sub[2-LOALARM] for storing Low Alarm value to test the MAIN-Value
#define HIALARM   3                   // Menu[#].Sub[3-HIALARM] for storing High Alarm value to test the MAIN-Value
#define ON        true                // Is the "Menu[#].Sub[??ALARM].State" (ALARM) ON or NOT-ON?

//---[ Globals ]-------------------------------------------------------------------------------------------------------
SSoftwareSerial IOSerial(SS_RX_PIN,SS_TX_PIN);              // SoftSerial for XBEE ( rxPin, txPin ) - allows interrupts
PeerIOSerialControl XBee(TRANSCEIVER_ID,IOSerial,Serial);   // XBee(ArduinoID, IOSerial, DebugSerial)
void GetItem(int i = -1);                                   // Predefine headers so SetupMenu() can be at top
void CheckAlarms(int i = -1);
void EEPROMGet(int i = -1);

volatile unsigned long last_bpress_millis = 0;              // Track last button press time
Button last_bpress = NONE;                                  // Store last button press for processing
Button prev_bpress = NONE;                                  // Used to count ButtonHeld counter
unsigned long wait_reply = 0;                               // Track non-blocking reply time
unsigned long last_iter_millis = 0;                         // Track last status iteration time

int idx = 0;                                                // Track Menu index item
int SubIdx = 0;                                             // Track current menu value item
int ButtonHeld = 0;                                         // Increment values by 10 when button is held
bool AlarmActive = false;                                   // Track if an Active Alarm is present
bool bIterating = false;                                    // Alarm only active while iterating the menu
int MenuItemsIdx = 0;                                       // Track the Menu Index (mi)
int PacketID = -1;                                          // For non-blocking communications
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

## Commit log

2017-02-02 Updates to Pump Controller and PDF manual added
    [Case.skp, Case.stl, CaseCover.skp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]
2017-02-08 Added Pump Controller
    [ArduinoStack.fzz, Case.skp, Case.stl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]
2017-03-18 Better Models
    [Case.skp, Case.stl, CaseCover.stl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]
2017-03-23 Many updates
    [Case.skp, Case.stl, HandRemote-BackCover.skp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]
2017-04-04 Removed battery power for Pump Controller
    [HandRemote-WiringDiagram.fzz, PumpController-AntennaCover.skp, PumpController-AntennaCover.stl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]
2017-04-27 Updated Remote Firmware and Sonic Water Level prints
    [Pers-Clamp.skp, Pers-Clamp.stl, Pers-ClampBraceBar.skp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]
2017-04-28 Fixed bug with Menu iterating out of bounds
    [HandRemote.ino]
2017-05-05 Smoothed edges, Fixed pressure, Updated manual
    [HandRemote-BackCover.skp, HandRemote-BackCover.stl, HandRemote-BatteryCover.skp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]
2017-05-10 Smoothed edges on models
    [HandRemote-BackCover.skp, HandRemote-BackCover.stl, HandRemote-BatteryCover.skp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]
2017-05-12 doc updates - Case fix
    [HandRemote-Case.skp, HandRemote-Case.stl]
2017-05-13 Moved pump select below battery menu item and updated doc
    [HandRemote-Buttons.skp, HandRemote-Buttons.stl]
2017-05-14 Pricing updates in doc - Fuller PumpController-Cover.stl
    [PumpController-Cover.skp, PumpController-Cover.stl]
2017-05-24 Battery alarm block at 550 for USB plug-in power
2017-06-27 New Design for a simpler and better build.
    [HandRemote-BackCover.skp, HandRemote-BackCover.stl, HandRemote-BatteryCover.skp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]
2017-06-28 Updated docs
    [HandRemote-BatteryCover-0.skp, HandRemote-WiringDiagram.fzz]
2017-07-01 Doc update and better Hand-Remote case fit
    [HandRemote-Case.skp, HandRemote-Case.stl]
2017-07-10 Sandbox - Started Pump-Controller LCD & PID operations.
2017-07-14 PID implemented in Sandbox
2017-07-14 Separated PID linked to other Menu Item for Manual or Automatic Control of that item.
2017-07-24 Sandbox - new class structure
    [PumpController-Case.skp, PumpController-Case.stl, PumpController-LCDCase.skp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]
2017-08-09 Sandbox - PID working
2017-10-02 Added docs Brochure.pdf
    [HandRemote-Buttons.skp, HandRemote-Buttons.stl]
2018-05-17 Fixed compile warnings for HandRemote
    Fixed compile warnings for HandRemote and added new sonic case
    [HydrometerCase.skp, HydrometerCase.stl, HydrometerCover.skp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]
2018-05-17 Final add
    [SonicHeadCover.skp]
2020-05-31 booklets added
    Printable booklets added
